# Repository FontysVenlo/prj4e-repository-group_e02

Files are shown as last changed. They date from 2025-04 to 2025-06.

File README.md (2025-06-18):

# Robot Duck
This repository holds the semester 4 embedded project - a robotic system that mimics duck's appearence and behaviour.

The structure is as follows:
- [Documentation](/documentation/) folder includes datasheets of the used components and document related deliverable files that we have used throughout the semester. 
- [Source](/src/DuckRobot/) folder with a software part of the project.

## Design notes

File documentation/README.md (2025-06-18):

# Documetation folder
In this folder you can find the documents that have been created and used during the project.

This includes:
- [3d Print files](/documentation/3dPrint/) - models used for printing.

- [Datasheets](/documentation/datasheets) - pdf datasheets of the used components, if existent.

- [Circuit](/documentation/circuit.md) - an electrical circuit layout and its progression throughout the semster.

- [Great Component List](/documentation/great-component-list.md) - a list of the components used and links for the corresponding suppliers.

- [Initial Project Idea](/documentation/initial-project-idea.md) - small and consise summary of the project idea at the very beginning.

- [Project Charter](/documentation/project4-charter-02.md) - more extensive information on requirements and scope of the project.

- [Retrospective Results](/documentation/retrospective-results.md) - a log with results from held retrospective meetings within the team.

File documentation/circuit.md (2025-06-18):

# Electrical Circuit

This document holds the circuit layout with version history and used microcontroller pins documentation.

- [Current Version](#current-circuit-diagram)
- [Version history](#version-history)
- [Pins](#components-and-pins)

## Current Circuit Diagram

**Main features:** microcontroller, speaker, compass, distance sensor are powered by 4S battery pack (6V) through a stepdown converter; Motors are powered with 2S LiPo batteries (7.4V) with implemented AD conversion for voltage tracking from one of the batteries. Both power sources are additionally protected with fuses - 400mA and slow 800mA repectively, - and are controlled with DPDT toggle switch.

Remarks:
- Only bridge the ground, power rows MUST NOT be bridged
- Due to the limited functionality of the tool, on diagram ground wires are colored blue, while the real life wires are black

Circuit Diagram
*Link to the project: https://app.cirkitdesigner.com/project/20f3ba8c-a90e-4b3a-8cf0-a0710fcb53cf*

## Version history

### Version 1: 
First rough draft only with initial components: microcontroller, compass, speaker module, distance sensor, servo motors and LiPo batteries connected in 2S.
V1

<br>

### Version 2:
Addition of second power source, intially planned 3S AA battery pack (4.8V), and two SPST (single pole single throw) toggle switches for both power circuits.
V2

<br>

### Version 3:
Move to the half breadboard, change of the second power source to 4S AA battery pack (6V) due to availability and, as microcontroller accepts only 5V input, addition of step-down converter. Change of singular toggle switches to DPDT (double pole double throw), as well as addition of two LEDs with PWM control.
V3

<br>

### Version 4:
Addition of the AD conversion from one of the LiPo batteries (3.7V) with usage of voltage divider (2 resistors).
V4

<br>

### Version 5 (Final):
Addition of two fuses for both power sources for additional safety measures.
V5

<br>

## Components and pins:
Currently free GPIO pins: 26, 4, 25, 36, 39, 35

<br>

Speaker [MP3](/documentation/datasheets/speaker-datasheet.pdf)

| Module Pin | Wire color | Controller Pin | 
|:---:|:---:|:---:|
| GND | Black | Ground row |
| VCC | White* | 5V row |
| TX | Grey | 19 |
| RX | Purple | 23 |

'*' - on diagram marked as red

<br>
<br>

Distance Sensor [HC-SR04](/documentation/datasheets/distance-datasheets.pdf)
| Module Pin | Wire color | Controller Pin |
|:---:|:---:|:---:|
| VCC | Red | 5V row |
| Trig | Pink | 13 |
| Echo | Green | 15 |
| GND | Black | Ground row |

<br>
<br>

Compass [CMPS2](/documentation/datasheets/compass-datasheet.pdf)

| Module Pin | Wire color | Controller Pin |
|:---:|:---:|:---:|
| VCC | Red | 3.3V |
| GND | Black | Ground row |
| SCL | Green | 22 |
| SDA | Pink | 21 |

<br>
<br>

 Servo Motors [Parallax](/documentation/datasheets/motor-datasheets.pdf) 
| Module Pin | Wire color | Controller Pin |
|:---:|:---:|:---:|
| GND | Black | Ground row |
| VCC | Red | 7.4V row |
| Pulse | White | 14 and 12 |

<br>
<br>

Red LEDs
| Module Pin | Wire color | Controller Pin |
|:---:|:---:|:---:|
| Cathnode | Black | Ground row* |
| Anode | Red - Orange | 2 |

'*' - through 220 ohm resistor

<br>
<br>

**AD conversion** takes pin 34 and requires 47K ohm (ground) and 12K ohm (in between) resistors.

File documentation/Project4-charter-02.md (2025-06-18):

# Project charter

### Embedded application – Duck
##### Author: group 2 <br> Location: Fontys University, Tegelseweg 255, 5912 BG Venlo <br> Version: v1.4  <br>  Date: 06.04.2025

## **Abstract:**
This project aims to develop an amphibious robotic duck that mimics the appearance and behaviour of a real duck while freeing of the need for animal care. Designed for outdoor ponds, it offers a lifelike alternative for the presence of a duck without the responsibilities of keeping one. By combining embedded systems with autonomous movement the project aims to create a functional, self-sustaining robotic companion for outdoor settings in order to replace ducks.

**Acronyms**

|**Abbreviation**|**Meaning**|
| :- | :- |
| KPI | Key Performance Indicator(s) |
| WBS | Work Breakdown Structure |

<br>
<br>

**Version history**

|**Version**|**Date**|**Comment**|
| :-: | :-: | :-: |
| 0\.1 | 14.03.2025 |First draft|
| 1.1 | 25.03.2025 | Initial chapters notes |
| 1.2 | 31.03.2025 | Chapters 1, 3, abstract, Introduction |
| 1.3 | 05.04.2025 | Chapters 2, 4, 7, WBS |
| 1.4 | 06.04.2025 | Chapters 5, 6 |

---

**Table of content** 

[1. Introduction](#1-introduction)

[2. Business case](#2-business-case)

[3. Approach](#3-approach)

[3.1 In scope](#3-approach)

[3.2 Out of scope](#3-approach)

[4. Deliverables](#4-deliverables)

[5. Quality management](#5-quality-management)

[6. Prerequisite](#6-prerequisite)

[7. Success criteria](#7-success-criteria)

[Appendix](#appendix)

[A: Work breakdown structure]( )

# 1. Introduction
The project focuses on designing and building a functional prototype capable of autonomous movement on water. The robotic duck will feature realistic behaviour such as floating, swimming, and quacking while maintaining energy autonomy for outdoor operation. Development efforts will include hardware design, embedded control systems, power and motor management, sensor integration, software implementation, etc. <br>
Over the course of the semester, the project will progress through research, hardware development, software implementation, and testing phases. The hardware will primarily cover essential materials, including motors, sensors, waterproofing components, and embedded processing units. Key challenges include ensuring waterproofing and durability, achieving lifelike movement and other behaviours, as well as balancing autonomous behaviour with potential user control.
By addressing these challenges and delivering a reliable, autonomous system, the project aims to create an innovative and practical robotic companion for outdoor environments.

# 2. Business case

There is currently no widely available robotic duck on the market that convincingly mimics the appearance and behaviour of a real duck. For pond owners and outdoor enthusiasts who wish to enjoy the presence of the bird without the responsibilities of caring for live animals, this project fills out the empty market gap. Robotic duck targets that gap, focusing on developing a lifelike amphibious robotic duck that can autonomously navigate water, respond to environmental changes in realtime, and produce realistic quacking sounds.

Besides its potential as a product with market prospects, this project also serves an important educational purpose. It provides a practical, hands-on opportunity to deepen developers' understanding of embedded systems, including areas such as motor control, sensor integration, wireless communication, and power management.

From an academic standpoint, the primary goal is to successfully complete and pass the Project 4 module. The amphibious robotic duck aligns well with the learning outcomes of the course, as it incorporates a broad range of embedded technologies and team collaboration. This combination of commercial potential and academic value makes the project both an intresting prototype and an effective learning platform.

# 3. Approach
The project will be conducted in a hybrid scrum way of working with a sprint length of 1 week. A Kanban board will be used to take track of all the use cases that have to be completed and a planning meeting will be used to plan the work for every sprint. Also daily stand up meetings will be used to keep every team member on track with the state of the project.
To achieve the projects objectives the project will be planned first by ordering and researching all the necessary components needed for the robot to function. On arrival of the components, the project team will use two project weeks with 20 hours of weekly working time to build actual initial hardware and at the end of the semester there will be additional 3 weeks of 40 hours of weekly working time to finish and complete the robot. Every other normal week a minimum of 5 hours will be spend working on the project.
### 3.1 In Scope 
The must have scope functionality of the duck robot includes:
- A working distance sensor that detects the shore
- An algorithm that turns the robot when it detects the shore and steers it into a different direction
- A driving system that lets the duck move straight with the help of a compass.
- A working speaker that plays different "Quack" sounds
- It needs to operate on its own for at least an hour
- A low power mode where the duck does not leave the shore anymore after finding it

The might haves include:
- A remote control that takes over the duck
- Movement on land
### 3.2 Out of Scope
- It will not be able to fly
- It will not be able to throw flames
- It will not be able to lay eggs
- It will not include a camera
- It will not be able to transition from water to ground
- It will not detect other ducks or interact with them

# 4. Deliverables 
The project will result in a set of defined deliverables, which represent the main outcomes of the development process. These deliverables serve as a mutual point of reference for project team members and other stakeholders to align expectations and track progress. The final results will reflect both the technical functionality and the organizational goals of the project.

### 4.1 Hardware and Component deliverables:
- A complete component list documenting all parts used in the final product, including motors, motor drivers, control modules, sensors, power units, and other relevant electronics or mechanical parts.
- A reusable power solution, rechargeable battery with efficient management and safety features.
- A distance sensor integrated into the final model in an optimal position to detect obstacles with high efficiency and accuracy.
- A speaker module playing preuploaded quacking tracks within reasonable volume range.
- A fully operational propulsion system for water-based enviroment with two Mississippi-type paddle wheels.
- An outer frame resembling a duck.

### 4.2 Software deliverables:
- Fully developed embedded software controlling autonomous behavior, sensor input handling, obstacle avoidance, sound playback, and power management logic.
- The code must be well-structured and maintainable, with proper commenting and implementation of software development design principles (e.g., single responsibility, separation of concerns, fail-safe logic).
- Implementation of a low battery mode, need for keeping the duck near the shore when battery charge falls below a critical level.
- Optional support for RC control.

### 4.3 Final Robot deliverable:
- Fully functional amphibious robotic duck, capable of operating autonomously on water, demonstrating stable navigation, sensor-based behavior, and basic interaction through sound.
- The robot capable of straight-line and manouvering movement, with the ability to adjust course automatically based on environmental input.
- All core systems should be sustained via onboard rechargeable battery power.
- The duck has a life-like visual appeal, fitting its intended use in outdoor ponds as a realistic animal alternative.
- The final model includes basic safety features, such as automatic shutdown in the event of critical faults or water damage detection.
- Supporting documentation delivered alongside the robot, including system schemas, wiring diagrams, component specifications, assembly instructions, and usage guidelines.

# 5. Quality management 
We are being evaluated on our project mainly through portfolio-based grading, so while it is nice to have the robotic duck working like it is intended.The focus is how we arrive there—how we experiment, what we discover, how we write it down on the way, and what we learn. 

### 5.1 Quality Goals

-The duck should be able to swim in water alone (or half-way alone at least) and perform programmed behavior.
-We want to make sure the key features, like movement, power, and code are working like intended.
-We have selected a lower voltage motor in order to save power consumption and total weight, which will ensure that our duck doesn't sink.
-We're also trying to get a good balance between the power supply's weight and how long it will propel the duck for.
-The plan is to do a lot of experimenting (such as trying different motor settings, wheel diameters, and power supply) and document what we find out to have a nice overview of our test results. This way we can improve the duck and find the perfect settings.

### 5.2 Quality Assurance

-We will start testing in smaller water containers like bathtubs or buckets before we move on to the "sea" on campus.
-Since waterproofing is a risky process, we will test the circuit separately outside of the duck first. That way, we won't be risking breaking equipment pieces too early.
-Every test, setup, and output that we do will be recorded in our team's GitHub repository, aswell as photos, comments, and observations too.

### 5.3 Quality Control

-With each test we perform, we'll check how well the duck can move, turn, and respond to commands.
-Before any water-test, we will check everything for waterproofing (visible and potentially in dunk tests) to ensure they are properly shut.
-When breaking something or getting it working incorrectly, we will write down or record that, work out what went wrong, and make changes before re-testing it.

### 5.4 Standards

-We're keeping our code clean and tidy and utilizing GitHub to track every branch, modification, and team feedback.
-Our team collaborates closely, sharing knowledge and keeping each other updated to ensure we're all involved and learning from every part of the project.

### 5.5 Team Roles

-Everyone is currently working on all aspects of the project. Like hardware, software, design, waterproofing, etc.
-If we ever do end up dividing the work later on, we'll still continue to inform each other so that all of us are aware of what's happening and can learn from each part of the project.

# 6. Prerequisite
There are some thinks which needs to be done tille we can completely start with building the robotic duck.

### 6.1 Parts and Components

-The university will be providing the ESP32 LoRa module. We haven't made all the details final for all aspects, but we did decide on a low-voltage motor so the build is light and is lower on power consumption.
-For power, we will explore a setup that has some combination of weight to runtime so the duck remains stable while running long enough to thoroughly test it.
-We will start with borrowed batteries from the university, and after we get a feel for what will work, we will purchase more suitable ones if needed.

### 6.2 Base Setup and 3D Printing

-We found an open-source design for the water wheels that looks good. We'll try it on and see how well it fits and works before committing.
-Our first tests will only use the plain duck base (no electronics) to see how it floats, how stable it is, and how much weight it can carry safely.

### 6.3 Control and Communication

-Wireless connection with the LoRa won't be important in this project. Autonomous movement is our top priority.
-For early testing, we’ll probably attach a rope to the duck so we can easily recover it. If everything works well, we’ll try adding remote control using RC modules later on.

### 6.4 Testing Environment

-We will start small—bathtubs, buckets, etc.—and work our way up to campus sea for full-scale testing.
-During early tests, we’ll also look at how much weight the base can handle before it becomes unstable or starts sinking.
-Safety of components is key—so we’ll avoid putting any electronics on the duck until we’re confident it can float reliably.

### 6.5 Risks

-There’s a chance things might go wrong in the water—like motors failing, the duck flipping, or waterproofing not holding up.
-Power issues (like weak batteries, unstable connections, or underpowered components) could also be a problem.
-To handle this, we’ll test things step by step, starting with the basics and building up once we’re confident in each part.

# 7. Success criteria
The success of the amphibious robotic duck project will be evaluated based on a set of measurable objectives, definitions of completion (acceptance criteria), and key performance indicators (KPIs). These criteria are intended to ensure that the system achieves its primary purpose — providing a life-like, self-operating duck for outdoor pond environments while performing safely in realistic conditions.

### 7.1 Measurable Objectives
The main measurable functionality of the robotic duck is its ability to autonomously navigate a water-based environment using the paddle-wheel system. This includes smooth movement, direction control, and responsive navigation. Additionally, onboard sensors must detect obstacles and enable the robot to avoid them in real-time without manual intervention. A built-in speaker module must also be capable of playing a selection of life-like quacking sounds to enhance realism.

For a more detailed breakdown of technical expectations refer to [Deliverables](#4-deliverables) chapter.

### 7.2 Acceptance Criteria
The project will be considered complete when the following conditions are met:
- The robotic duck maintains stable movement on water and can adjust its trajectory based on data from onboard obstacle detection sensors.
- The system is capable of operating for at least 60 minutes on a single charge under average load conditions, including motor and sensor activity.
- The software supports secondary modes, such as a low battery mode, which automatically limits operation and keeps the duck near the shoreline once power drops below a predefined threshold.
- The duck emits quacking sounds at realistic intervals to simulate the presence of a real duck.

### 7.3 Key Perfromance Indecators
Software Performance: 
- All autonomous behaviors (navigation, low-battery fallback) must pass simulated and real-world test cases with ≥ 90% consistency.
- Control system must maintain a response time below 200 ms in manual mode.

Hardware Performance:
- Motors maintain operation within ±10% of the expected RPM under normal conditions.
- Obstacle detection system has an accuracy of ≥ 95% within the 0.5–2 meter range.
- Motor temperature stays below X°C during prolonged use (value to be defined through testing).

Operational Success:
- The duck must maintain floating position and movement stability in at least 85% of tested water conditions (e.g., small waves, uneven pond surfaces).
- The robot must successfully complete an autonomous navigation, demonstrating at least 80% success rate in obstacle avoidance scenarios during test runs.

# Appendix 
### Appendix A: Work Breakdown Structure 
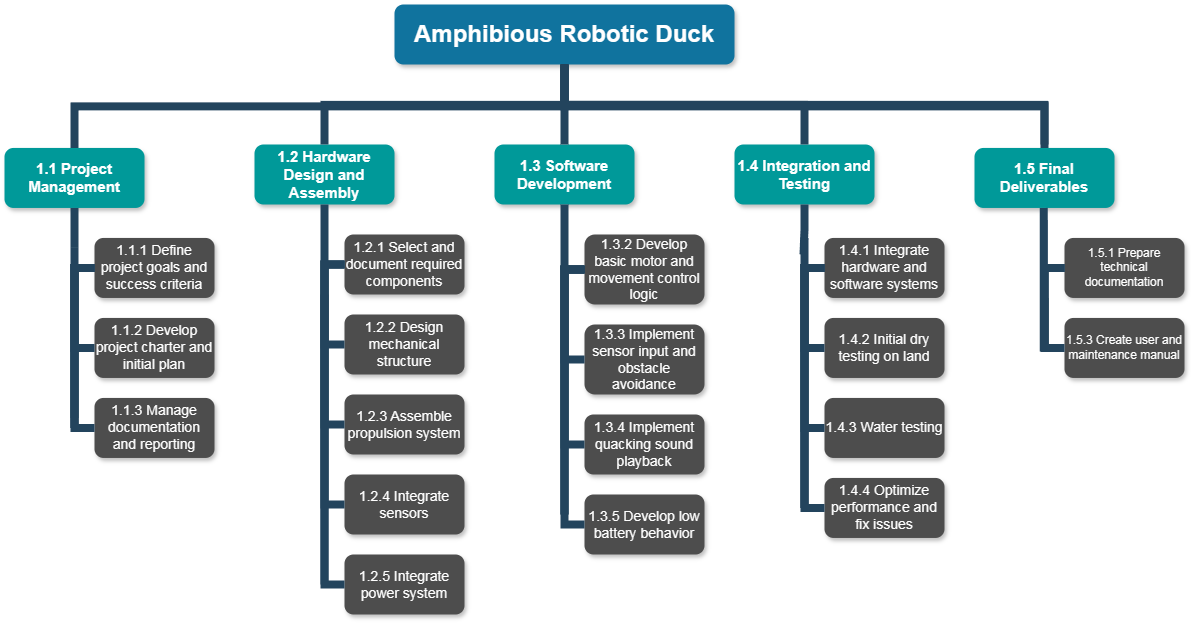
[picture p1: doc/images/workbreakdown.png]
Work


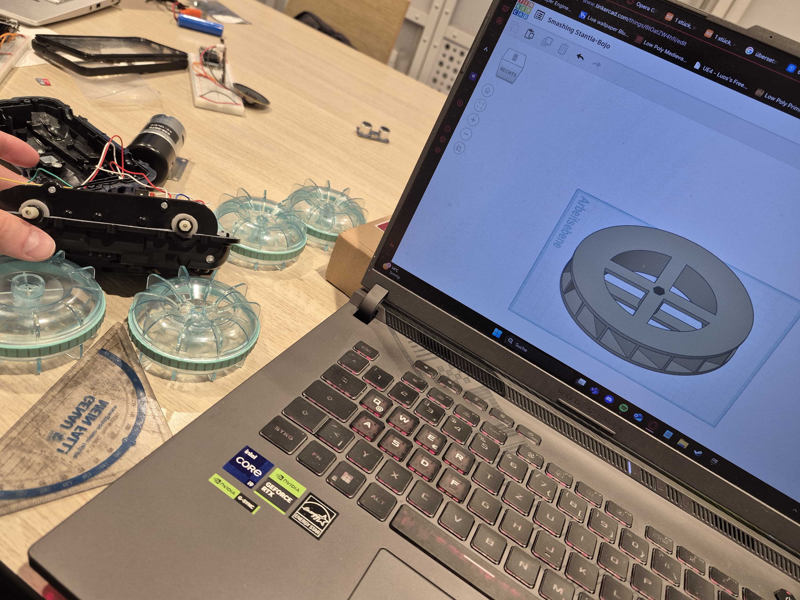
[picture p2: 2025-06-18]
documentation/images/PRJ_week_2/Design_first_waterwheeldraf_2.jpeg

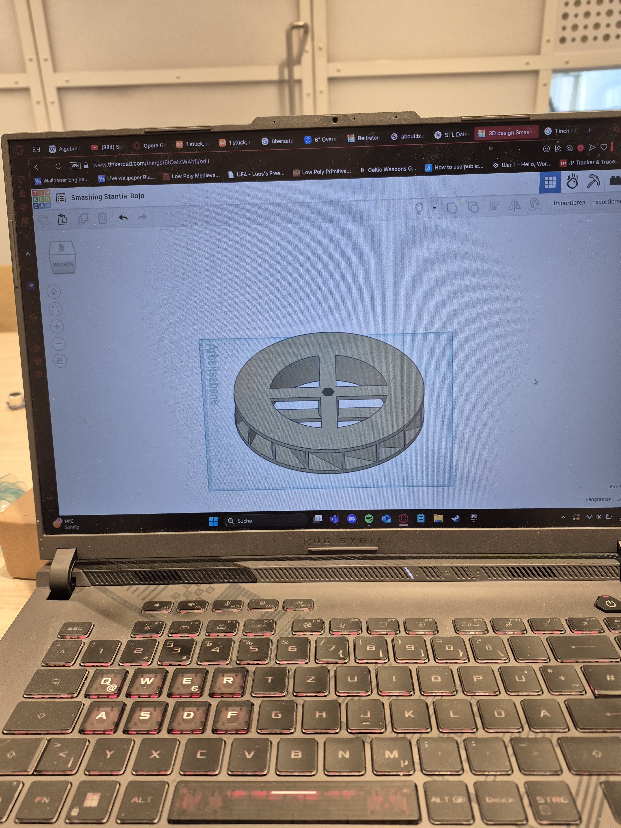
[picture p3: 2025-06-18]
documentation/images/PRJ_week_2/Designing_first_waterwheeldraft.jpeg

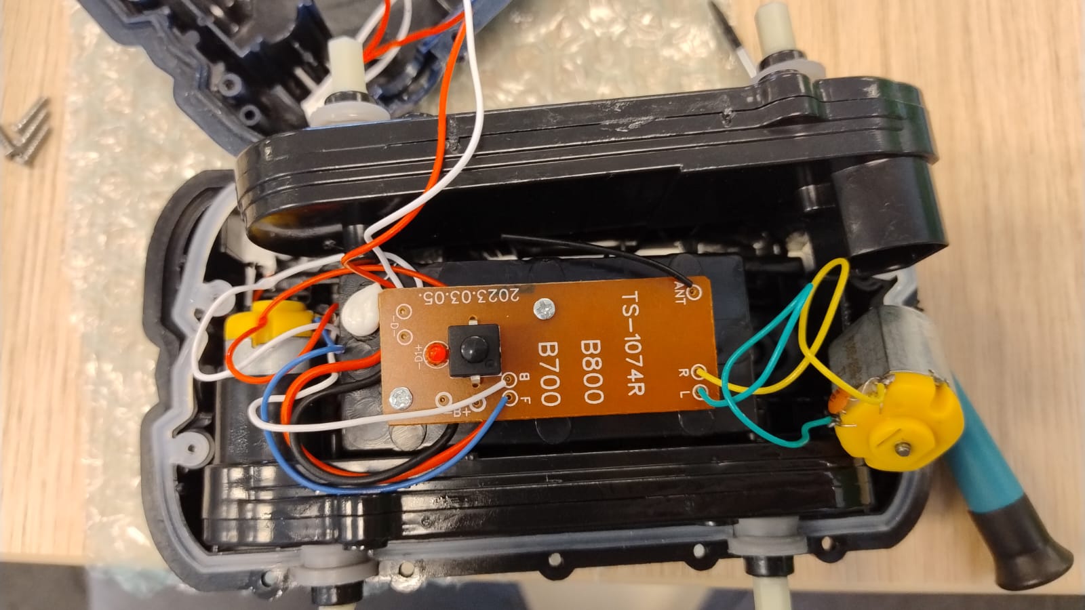
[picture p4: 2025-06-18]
documentation/images/PRJ_week_2/Toy_inside.jpeg

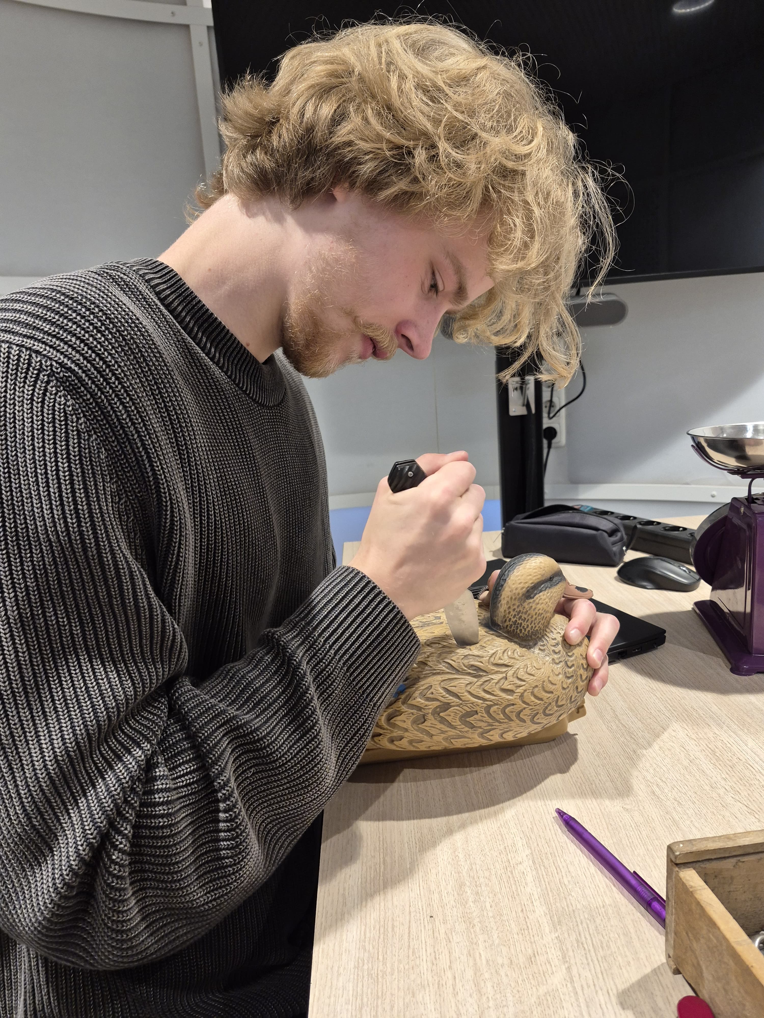
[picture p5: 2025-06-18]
documentation/images/PRJ_week_2/Cutting_duck.jpeg

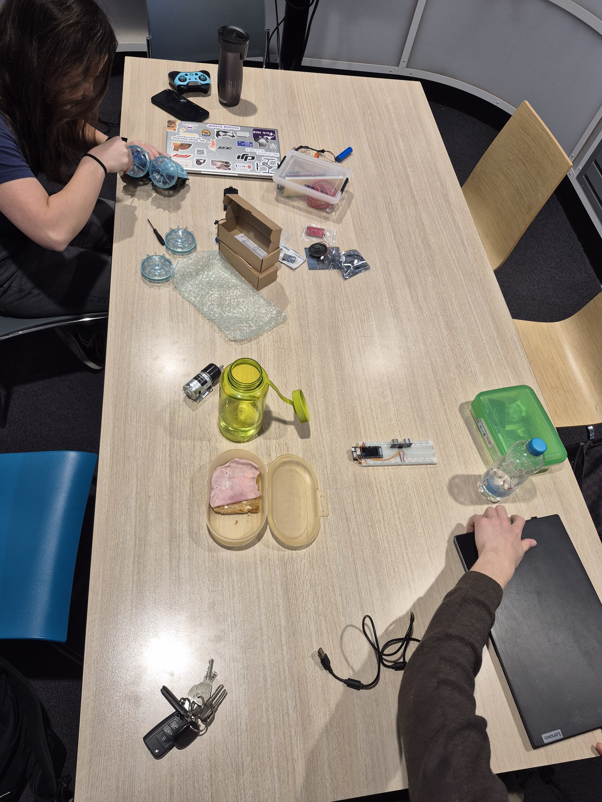
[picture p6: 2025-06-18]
documentation/images/PRJ_week_2/Working_on_toy.jpeg

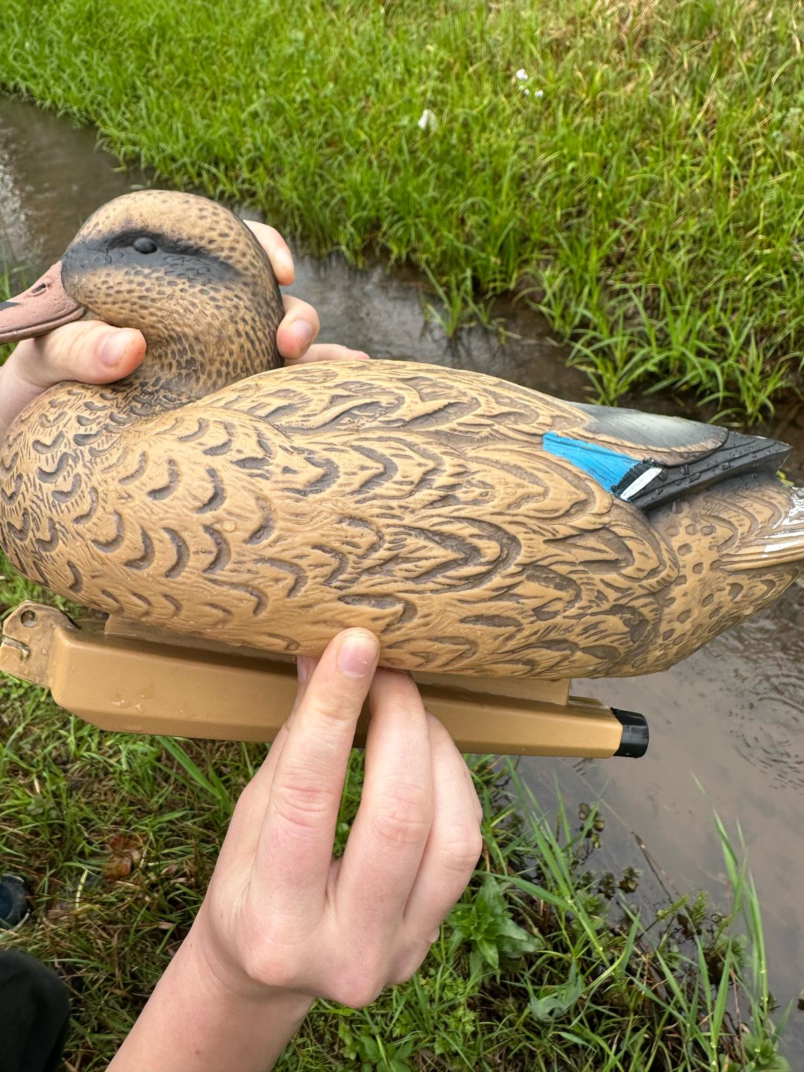
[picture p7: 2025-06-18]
documentation/images/PRJ_week_2/Duck_waterline_with_weight.jpeg

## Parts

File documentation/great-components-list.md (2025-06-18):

# Final Components

| Item | Category | Module Name | Supplier | Number to be ordered | Price per stuck | Link | Status |
|:----:|-----|-----|-----|:-----:|:-----:|-----|-----|
| 1 | Speaker-Module | Open-Smart MP3 | Tiny-Tronics | x1 | €7.50 | [Tinytronics](https://www.tinytronics.nl/en/audio/audio-sources/open-smart-mp3-module-with-speaker) | Delivered|
| 2 | Compass | Digilent Pmod CMPS2 | RS-online | x1 | €7.87 | [RS-online](https://nl.rs-online.com/web/p/sensor-development-tools/1947661?gb=s) | Delivered 
| 3 | Step down converter | Pololu 5V D30V30F5 | Robotshop | x1 | €14.92 | [Robotshop](https://eu.robotshop.com/products/pololu-5v-step-down-voltage-regulator-d30v30f5-34a-continuous-output) | Delivered |
| 4 | Motor | Parallax SERVOMOTOR RC 120 RPM 6V | DigiKey | x2 | €25.82 | [DigiKey](https://www.digikey.nl/en/products/detail/parallax-inc/900-00360/7707660) | Delivered |
| 5 | Microcontroller | LilyGo TTGO T3 LoRa32 | TinyTronics |  x2 | €22.00 | [Tinytronics](https://www.tinytronics.nl/en/development-boards/microcontroller-boards/with-lora/lilygo-ttgo-t3-lora32-868mhz-v1.6.1-esp32) | Delivered |
| 6 | Motor Driver (optional*) | Pololu TB6612FNG DUAL MOTOR DRIVER| DigiKey | x2 | €4.57 | [DigiKey](https://www.digikey.nl/en/products/detail/pololu/713/10450399?s=N4IgTCBcDaICoCEBsSCMYBiA5A4iAugL5A) | Delivered |
| 7 | Batteries | LiPo 3.7V battery 2500mAh  | Conrad | x2 | €24.59 | [Conrad](https://www.conrad.nl/nl/p/akyga-lp475085-accupack-batterijgrootte-speciaal-lipo-3-7-v-2500-mah-3385860.html) or similar | Delivered |

### Added later / Not for ordering

| Item | Category | Module Name | Link |
|:----:|---|---|---|
| 8 | Toggle Switches | MSP-1 SPST | [Mouser](https://eu.mouser.com/ProductDetail/Carling-Technologies/2S1-MSP1-T3-B2-M6QE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) |
| 9 | Batteries | 3AAA pack 4.8V | |
| 10 | Distance Sensor | HC-SR04 | [TinyTronics](https://www.tinytronics.nl/nl/sensoren/afstand/ultrasonische-sensor-hc-sr04) |

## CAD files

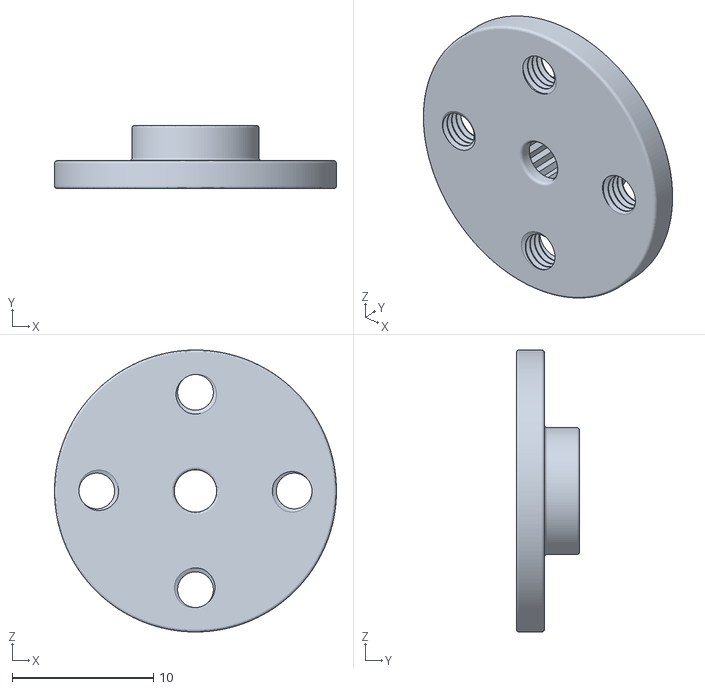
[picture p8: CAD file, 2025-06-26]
documentation/3dPrint/servo_horn.stl
20.0 x 4.50 x 20.0

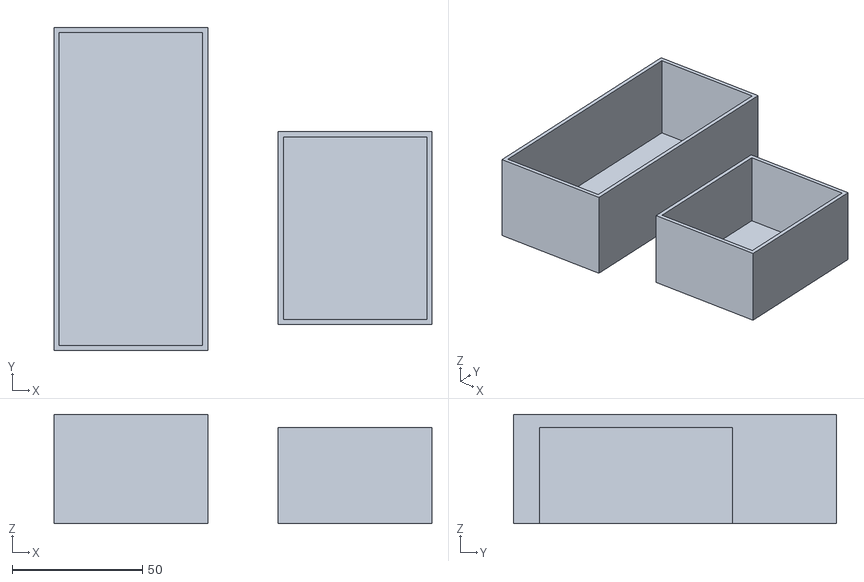
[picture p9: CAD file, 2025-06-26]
documentation/3dPrint/Duckboxes.stl
145.0 x 124.0 x 42.0

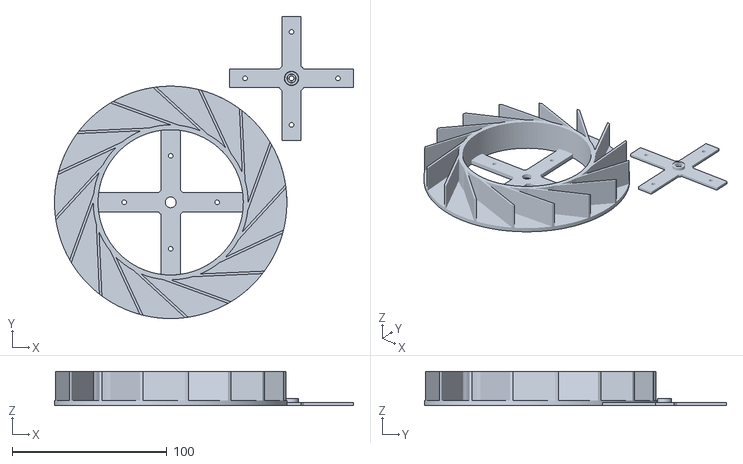
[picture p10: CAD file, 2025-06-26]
documentation/3dPrint/Ready to Print Wheel + Adapter (3).stl
193.0 x 195.0 x 22.0

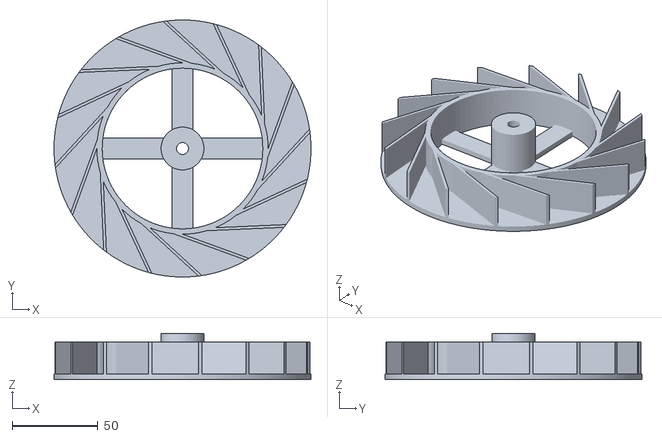
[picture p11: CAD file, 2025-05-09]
documentation/3dPrint/Waterwheel_v2.1.stl
150.0 x 150.0 x 27.0

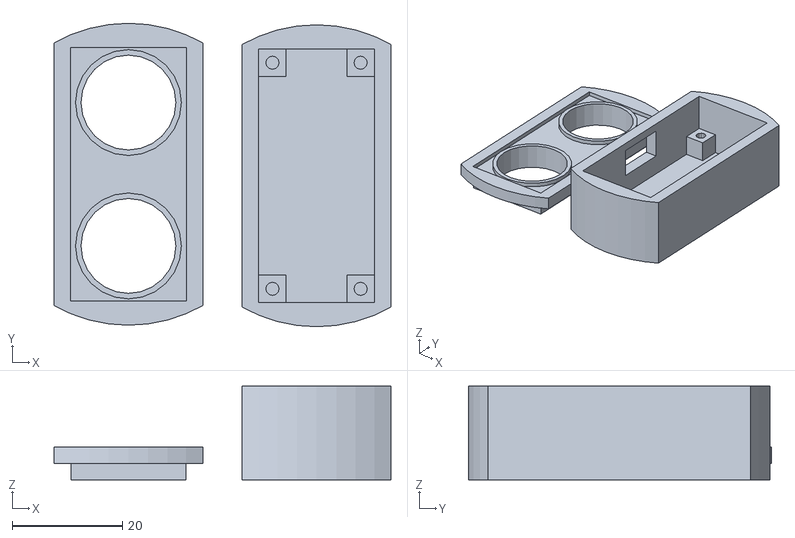
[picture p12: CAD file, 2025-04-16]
documentation/3dPrint/HC-SR04_my_Case_both_Parts.stl
61.1 x 55.0 x 17.0

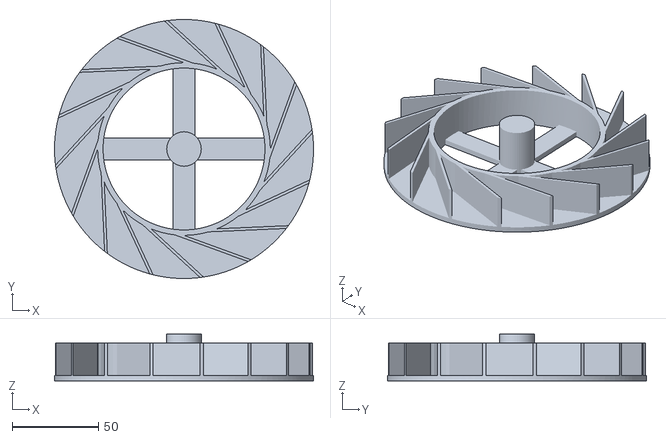
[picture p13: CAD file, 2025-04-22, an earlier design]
documentation/3dPrint/Waterwheel_v2.0.stl
150.0 x 150.0 x 27.0

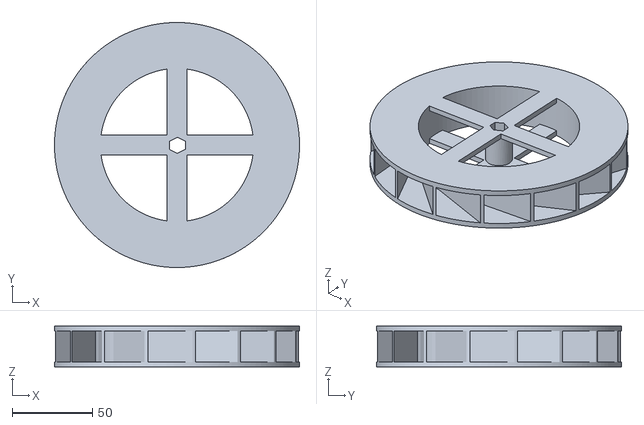
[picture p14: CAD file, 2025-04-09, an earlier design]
documentation/3dPrint/Waterwheel_v1.0.stl
152.4 x 152.4 x 25.4

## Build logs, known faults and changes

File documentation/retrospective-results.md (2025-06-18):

# Retrospective Meetings results
While we did not follow a full agile methodology, we used several agile principles to support smooth development and reflection. Our first retrospective meeting was held in Week 8, and a second is planned for the final project weeks. The long interval between retrospectives is explained by the unique nature of embedded systems projects and the way project weeks are distributed throughout the semester.

### Week 8 - Project Weeks 1–2
During our retrospective meeting in Week 8, we reflected on the early stage of the project, especially the first two project weeks. Overall, the group agreed that the progress was good, despite a few delays and changing scope.

The main challenge was the late delivery of hardware components, which limited hands-on work. However, we made the most of the available time by focusing on software preparation, electrical circuit planning, and testing individual components where possible.

Hardware research took more time than initially estimated, especially around motor selection and sources of power. While we had most of the scope defined, it kept changing due to our lack of awereness of possible options. The research resulted in several design changes but helped forming better-informed decisions. Hovewer, it should have been documented better both for the evidence andjustification of our choices later in the future.

We expect the visible progress to slow down temporarily, as the next stage involves preparation for full assembly and systems integration. Many results (e.g., propulsion, navigation, power behavior) will only become seen once the physical assembly is in process. This being said, we should breakdown the intermediate tasks into smaller scopes (e.g "Motors software implementation" into "Motors Software - Normal Mode", "Motors Software - Low Battery Mode", "Motors Software - Integration", etc). This way the progress will feel more real despite not having physical model yet fully working.

### Week 14 - last project weeks
During our second retrospective meeting in Week 14, we reflected on the final part of the project, focusing on the outcomes of the last few weeks and our overall group performance. Despite facing several challenges, we completed all must-have features on time and saw improvements in team coordination.

One area that could have been improved was the inconsistent use of the project board. While helpful at first, it became less reliable due to delayed updates and overly general task descriptions. This led to less effective use of the tool. A more structured and regularly updated task board would have supported better collaboration and more balanced task distribution across the team.

We also made several technical decisions late in the process, including changes to the electrical circuit. With better planning, we could have avoided the extra stress and saved both time and effort. Looking back, we should have allocated more time for safety considerations and potential last-minute changes.

Another problem was the uneven distribution of work across different areas. While having specialization is natural, it resulted in some team members having fewer deliverables in certain areas, making it harder to show evidence of their progress. For future projects, we will assign subtasks more attentively so that everyone can contribute in each area.

On the positive side, our group communication remained strong, and discussions during stand-up meetings helped us stay aligned throughout the project. We improved in time management and individual leadership, especially in leading the stand-ups. Additionally, as the semester progressed, we became much more confident with the tools and hardware, leading to greater efficiency and more informed decision-making.

Lastly, we realized the importance of documenting feedback and design decisions more clearly. Some changes and workarounds were made on the spot but weren’t properly recorded, which made it difficult to trace decisions later. The same applied to feedback — on several occasions, we failed to document it timely and had to do so later, often missing important details.

Despite these challenges, we are proud of the progress we made and how we adapted to difficulties. We gained experience working on a real-world embedded systems project, where unpredictable and hardware-related problems are part of the process. We all agree, in the case of a similiar project we would be able to complete it way faster and more efficiently, highlighting that the learning curve we went through significally increasing our knowledge.

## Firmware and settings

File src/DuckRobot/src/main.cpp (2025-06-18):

#include <Arduino.h>
#include "soundManager.h"
#include "movementLogicManager.h"
#include "compassManager.h"
#include "pwmEyesManager.h"

#define LED 25

void heartbeat(void *parameter);

void setup() {
  // put your setup code here, to run once:
  Serial.begin(115200);
  pinMode(LED, OUTPUT);

  // hearthbeat thread
  xTaskCreate(
      heartbeat,   // Function that should be called
      "heartbeat", // Name of the task (for debugging)
      4096,        // Stack size (bytes)
      (void *)LED, // Parameter to pass
      1,           // Task priority
      NULL         // Task handle
  );

  // soundManager thread
  xTaskCreate(
      start,       // Function that should be called
      "soundTask", // Name of the task (for debugging)
      4096,        // Stack size (bytes)
      NULL,        // Parameter to pass
      1,           // Task priority
      NULL         // Task handle
  );

  // movementLogicManager thread
  xTaskCreate(
      startMovement,  // Function that should be called
      "movementTask", // Name of the task (for debugging)
      4096,           // Stack size (bytes)
      NULL,           // Parameter to pass
      1,              // Task priority
      NULL            // Task handle
  );

  // compassManager thread
  xTaskCreate(
      startCompass,  // Function that should be called
      "compassTask", // Name of the task
      4096,          // Stack size (bytes)
      NULL,          // Parameter
      1,             // Task priority
      NULL           // Task handle
  );

  xTaskCreate(
      setupPWM,  // Function that should be called
      "pwmEyes", // Name of the task (for debugging)
      4096,      // Stack size (bytes)
      NULL,      // Parameter to pass
      1,         // Task priority
      NULL       // Task handle
  );

  // threads to be added...
}

void loop() { }

void heartbeat(void *parameter) {
  // use internal (onboard) led as heartbeat monitor
  int led;
  led = (int)parameter;
  for (;;)
  { // infinite loop
    // Turn the LED on
    digitalWrite(led, HIGH);
    // Pause the task for 500ms
    vTaskDelay(500 / portTICK_PERIOD_MS);
    // Turn the LED off
    digitalWrite(led, LOW);
    // Pause the task again for 500ms
    vTaskDelay(500 / portTICK_PERIOD_MS);
  }
}

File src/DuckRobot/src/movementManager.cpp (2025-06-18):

#include <Arduino.h>
#include "movementManager.h"

#define motorPin1 12  // white
#define motorPin2 14

// Settings PWM
#define pwmChannel 0
#define pwmChannel2 1
#define pwmFreq 50       
#define pwmResolution 16
#define centerPulse 4915
#define maxSpeed 205 // 820 max speed

int delta = 40; //to understand why 20 pls look at the datasheet average rotational velocity graph
volatile int state = 0;

void handleState();
void move();
void stop();
void turn();

void startMovementManager(void * parameter) {
    // PWM
    ledcSetup(pwmChannel, pwmFreq, pwmResolution);
    ledcAttachPin(motorPin1, pwmChannel);
    ledcSetup(pwmChannel2, pwmFreq, pwmResolution);
    ledcAttachPin(motorPin2, pwmChannel2);
  
    vTaskDelay(2000 / portTICK_PERIOD_MS);
    // Serial.println("Start motors");
    handleState();
}  

void handleState(){
    for (;;) {
        if (state == 1){
            move();
        }else if(state == 2){
            turn();
        }else if(state == 3){
            stop();
        }
    }
}

void move() {
    // anti clock wise
    ledcWrite(pwmChannel2, centerPulse + delta);
    //clock wise
    ledcWrite(pwmChannel, centerPulse - delta);
    // Serial.println("Forward start");
    
    if (delta < maxSpeed)
    {
        delta += 2;
    }
    vTaskDelay(20); 
}

void turn(){
    ledcWrite(pwmChannel, centerPulse + maxSpeed);
    ledcWrite(pwmChannel2, centerPulse + maxSpeed);
    // Serial.println("Forward");
    vTaskDelay(20);
}

void stop(){
    delta = 40; //to understand why 20 pls look at the datasheet average rotational velocity graph
    ledcWrite(pwmChannel, centerPulse);
    ledcWrite(pwmChannel2, centerPulse);
    // Serial.println("Stop");
    vTaskDelay(20);
}

//should maye use vTaskDelay(1) when able to test out

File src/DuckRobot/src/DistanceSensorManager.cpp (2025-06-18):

#include <Arduino.h>
#include "distanceSensorManager.h"
#include <Wire.h>

#define trigger 13
#define echo 15

float distance = 9999;

void startDistanceSensor(void * parameter){
    pinMode(trigger, OUTPUT);
    pinMode(echo, INPUT);

    for(;;){
        long duration;

        digitalWrite(trigger, LOW);
        delayMicroseconds(2);

        digitalWrite(trigger, HIGH);
        delayMicroseconds(10);
        digitalWrite(trigger, LOW);

        duration = pulseIn(echo, HIGH);
        distance = duration * 0.034 / 2;
        delay(100); 
        Serial.print("Distance: ");
        Serial.println(distance);
    }
}

float getDistance(){
    return distance;
}

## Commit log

2025-03-29 found a cooler speaker module that already has an sd slot and also likely makes life easier
2025-04-09 First Version of the waterwheel
    First Version of the waterwheel with 1cm Polygon in the middle
    [Waterwheel_v1.0.stl]
2025-04-10 added basic thread structure and connected it to the soundManager
2025-04-10 fixxed some minor errors I did before
    [main.cpp, movementManager.cpp]
2025-04-16 Ultrasonic sensor box
    3d module of a housing for the ultrasonic sensor
    [HC-SR04_my_Case_both_Parts.stl]
2025-04-22 New version of Waterwheel
    Changes made for the Water wheel:
    -open on the top so we can print without support
    -change the adapter in the middel according to the new motor
    [Waterwheel_v2.0.stl]
2025-05-09 motors code
2025-05-09 Newest version of the waterwheel
    newest version of the water wheel for the new motor
    [Waterwheel_v3.0.stl]
2025-05-12 Repo restructure + circuit
    [HC-SR04_my_Case_both_Parts.stl, Waterwheel_v1.0.stl, Waterwheel_v2.0.stl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]
2025-05-13 Fix circuit model
2025-05-26 Circuit diagram v2 toggle / 2nd power
2025-06-05 added pwm eyes
2025-06-06 Rename Unbenanntes Video – Mit Clipchamp erstellt (1).mp4 to Weighttest
2025-06-10 Circuit, adc, pwm
2025-06-12 changed the motor steering to better real time movement
    also the motor starts slow now and goes gradually faster. also the sound module chooses out of 20 and not 10 mp3 files now
2025-06-12 Circuit documentation
2025-06-26 add missing models
    [Ready to Print Wheel + Adapter (3).stl]
